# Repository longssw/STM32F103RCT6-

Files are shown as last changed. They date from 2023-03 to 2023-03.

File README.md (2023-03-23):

输入图片说明

# STM32F103RCT6小车主控板

> 参考项目:[【自制】ROS机器人四电机驱动控制板_哔哩哔哩_bilibili](https://www.bilibili.com/video/BV1tR4y1w7xe/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)
>
> 开源链接：https://github.com/fan-ziqi/My_ROS_Robot

## 0.关于本项目

一款高集成度的小车主控板,这是基于开源项目修改而来的作品。将原本0402封装的部分阻容更换成0603更加便于焊接，制作成本大概在160~200元之间（部分元件价格波动较大导致）。

额外IO资源
| 引脚 | 特殊功能 | 引脚 | 特殊功能 |
| ---- | --- | ---- | --- |
| PA4  | ADC4 | PA12 | --- |
| PA5  | ADC5 | PB12 | --- |
| PA6  | ADC6 | PB13 | TIM1CH1  |
| PA7  | ADC7 | PC15 | --- |
| PA8  | --- | PC13 | --- |
| PA11 | TIM1CH4  | PC14 | --- |
| PB10 | TX3 | PB11 | RX3 |
| PC10 | TX4 | PC11 | RX4 |

## 1.硬件说明

### 焊接顺序

1. 开关电源 如果输出5V不正常就不用继续焊下去了(集成开关电源经常翻车,心态放好就行)。
2. 线性稳压电源 5转3.3这个一般不会翻车。
3. CP2102和typec口 焊接成功之后插入电脑可以找到CP2102的串口就表示成功。
4. STM32芯片 焊好之后可以通过USB一键下载。
5. MPU6050 如果无法读取数据的话检查是否虚焊(陀螺仪很容易虚焊,不要慌,趁现在器件还不是很多修补起来还是很容易的)。
6. TB6612和剩余器件。

如果你走完了上述步骤，则恭喜你获得一块小车主控板。

下面是我遇到的一些问题和解决办法：

1. 如果焊接完成以后发现单片机的速度比正常的慢了好几倍，可以检查一下晶振以及它旁边的两个电容有没有焊好。（内部RC振荡器的精度通常比用HSE（外部晶振）要差上十倍以上）
2. 接12V的时候注意看清楚正反，本人有幸冒过几次烟~

### 开关电源选择

常用的12转5开关电源有如下几款

| 型号 | 温度（3A） | 效率（3A） |
| --- | --- | --- |
| MP2236  | 57.5℃ | 96% |
| MP2225  | 82.2℃ | 94% |
| MP2315S | 115℃ | 90% |

BOM表差异

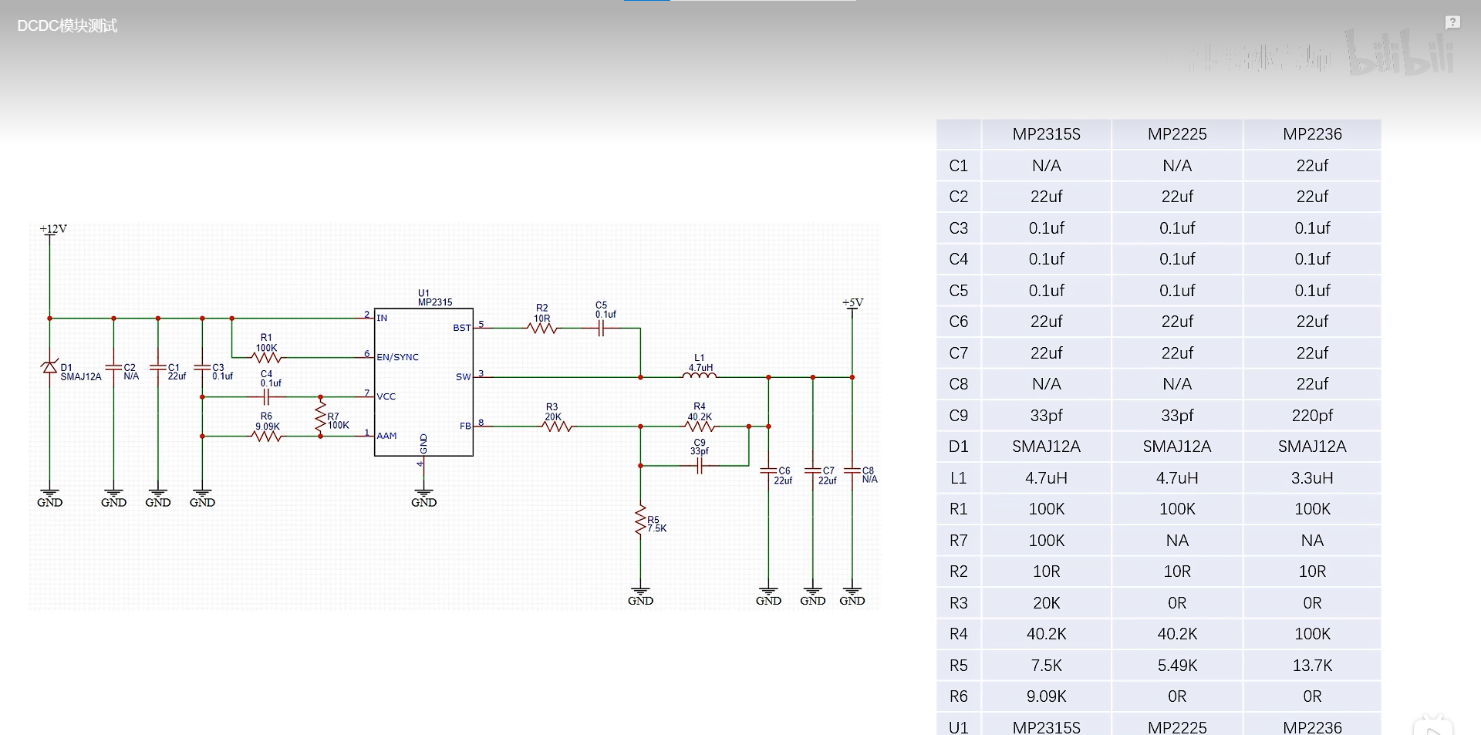
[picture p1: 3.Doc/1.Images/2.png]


具体可以看工科男孙老师的测评

[如何让你的电源模块更强大 滤波电容越大越好嘛？_哔哩哔哩_bilibili](https://www.bilibili.com/video/BV1XQ4y1Q74n/?spm_id_from=333.788&vd_source=1ef309ff3be99d9dd05b8566251abc3d)

### 串口自动下载电路

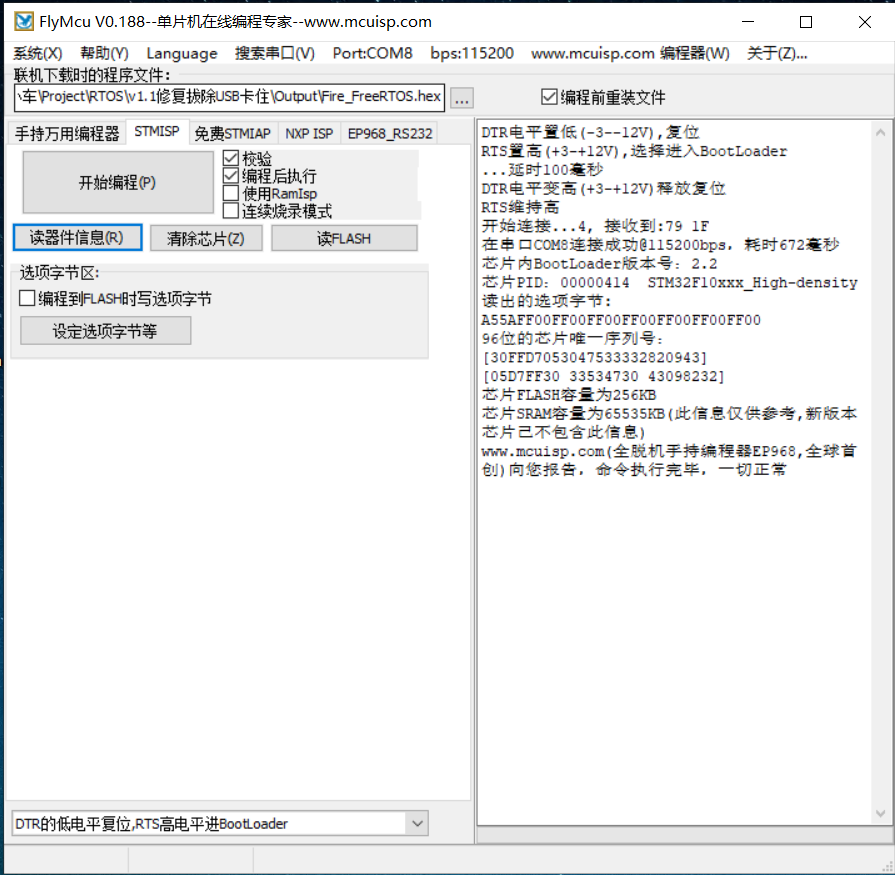
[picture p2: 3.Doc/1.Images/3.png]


## 2.软件说明

软件现在尚未完成,敬请期待

## 3.后话

小小吐槽一下原作者,把PC12,PD2这个串口5拿去点灯了，太奢侈了呜~

有什么问题欢迎留言讨论,共同进步!

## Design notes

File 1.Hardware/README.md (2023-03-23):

修改记录:

1.2023-1-29

+ 修改三角拨动开关孔大小 

  孔径1.7mm 焊盘2.5

  适配SS12D06三角拨动开关

+ 修改了些许错误丝印

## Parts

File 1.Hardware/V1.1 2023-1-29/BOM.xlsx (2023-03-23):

ID | Name | Designator | Footprint | Quantity
1 | AMS1117-3V3 | AMS1 | SOT223 | 1
2 | 22uf | C1, C2 | C1206 | 2
3 | 0.1uf | C3, C4, C5, C12, C13, C14, C28, C29 | C0603 | 8
4 | 22uf | C6, C7, C8 | C0805 | 3
5 | 220pf | C9 | C0603 | 1
6 | 20pf | C10, C35 | C0603 | 2
7 | 0.1uf | C11, C17, C19, C21, C22, C23, C24, C25, C26, C31, C32, C34 | C0603 | 12
8 | 10uf | C15, C16,C18, C20 | C0603 | 4
9 | 22uf | C27, C30 | C0603 | 2
10 | 2.2nf | C33 | C0603 | 1
11 | SMAJ12A | D1 | SMA | 1
12 | 1N4148 | D2, D3, D4 | SOD-323 | 3
13 | HDR-1X6 | EM1, EM2, EM3, EM4 | XH2.54-LI-6P | 4
14 | MSMD200-8V 2A | F1 | FU 0603 | 1
15 | HDR-1X7 | JP1, JP2, JP3 | HDR2.54-LI-7P | 3
16 | Header 8X2 | JP_EX | HDR2.54-LI-2x8P | 1
17 | HDR-1X4 | JP_PI | HDR2.54-LI-4P | 1
18 | HDR-1X4 | JP_SWD | XH2.54-WI-4P | 1
19 | TACT 4P | K1, K2, K3 | SW-SMD_4P-L4.2-W3.3-P2.15-LS5.1 | 3
20 | 3.3uH | L1 | L-SMD-0630 | 1
21 | LED | LED_BLUE, LED_GREEN, LED_PW | LED0603 | 3
22 | MP2236 | MP2236 | TSOT23-8_MP2225_MNP | 1
23 | SS8050 | Q1 | SOT23-3N | 1
24 | SS8550 | Q2 | SOT23-3N | 1
25 | 100K | R1, R4 | R0603 | 2
26 | 10R | R2 | R0603 | 1
27 | 0R | R3, R6 | R0603 | 2
28 | 13.7K | R5 | R0603 | 1
29 | N/A | R7 | R0603 | 1
30 | 4.7K | R8, R10, R18, R20 | R0603 | 4
31 | 10K | R9, R11, R12, R14, R21 | R0603 | 5
32 | 1M | R13 | R0603 | 1
33 | 1K | R15, R16, R17, R22, R23, R24 | R0603 | 6
34 | 1K | R19 | R0603 | 1
35 | 5.1K | R25, R26 | R0603 | 2
36 | 4.7K | RP12, RP34 | RCA-8P4R-0603 | 2
37 | SS-12F23 | S1 | SS-12D10 | 1
38 | CP2102 | U1 | QFN-28 | 1
39 | STM32F103RCT6 | U2 | LQFP64_N | 1
40 | MPU6050 | U3 | QFN-24 | 1
41 | TB6612FNG | U4, U5 | SSOP24_M | 2
42 | Type-C | USB1 | Type-C-TOP | 1
43 | HDR-1X2 | VIN1 | KF301-5.0-2P | 1
44 | 8M | X1 | OSC 3225-4P | 1
